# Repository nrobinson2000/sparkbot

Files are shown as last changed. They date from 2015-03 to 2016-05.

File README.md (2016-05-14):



# SparkBot: The IoT robotics kit for everyone

SparkBot is a robotics kit designed for makers and hobbyists, recommended for individuals aged 12 and up. It uses the Photon by Particle to teach C++ and principles of the Internet of Things. Its goal is to teach functional robotics, Arduino, and REST API's in an understandable method.

The purpose of SparkBot is to create a robot front end for the Photon that will get people excited to program and make projects with. It will give a reason for people to become interested in the Internet of Things by creating an exciting interactive experience.

SparkBot is a two part product. Although it uses both hardware and software from Particle, unique PCBs and 3D printed bodies must be produced. SparkBot also has its own software library with custom C++ functions to improve the SparkBot programming experience.

# The Photon:

The Photon is the SparkBot's brain. It runs C++ on its micro operating system, that communitcates with Particle's servers to create a low cost, high power device. Code can be uploaded to the Photon in several ways. Flashed from the [Particle.io web IDE][7], uploaded from either the Particle DEV IDE or the Particle CLI tool, or compiled locally and flashed over USB serial.

The Photon is Particle's second IoT development board. Their first was the Core, a huge Kickstarter success. The Photon was developed without any Kickstarter support, and the Electron, their third board, which uses celluar technology, was successfully funded on Kickstarter this year.

# Licensing:

SparkBot respects and uses many open source technologies and services. All of the software sources and hardware files can be found on GitHub.

[][8]  
SparkBot by [Nathan Robinson][9] is licensed under a [Creative Commons Attribution-NonCommercial-ShareAlike 4.0 International License][8].  
Based on a work at [https://github.com/nrobinson2000/sparkbot][2].

# Repositories:

SparkBot is organized into two repositories. One for the C++ library, and the other for everything else, including the hardware files, plans and images.

If you are looking for the C++ library for SparkBot, head over to [https://github.com/nrobinson2000/sparkbot-default][10]. The main repository is located at [https://github.com/nrobinson2000/sparkbot][2].

It is likely that a third repository will be created for the SparkBot documentation.

# Included in the SparkBot Kit:

* 1 Particle Photon
* 1 Micro usb cable
* 1 Half Breadboard
* 1 Fully assembled Robot body
* 10 Jumper wires
* 1 Protective travel case
* 1 User manual and quickstart guide

# Photon Pinout:
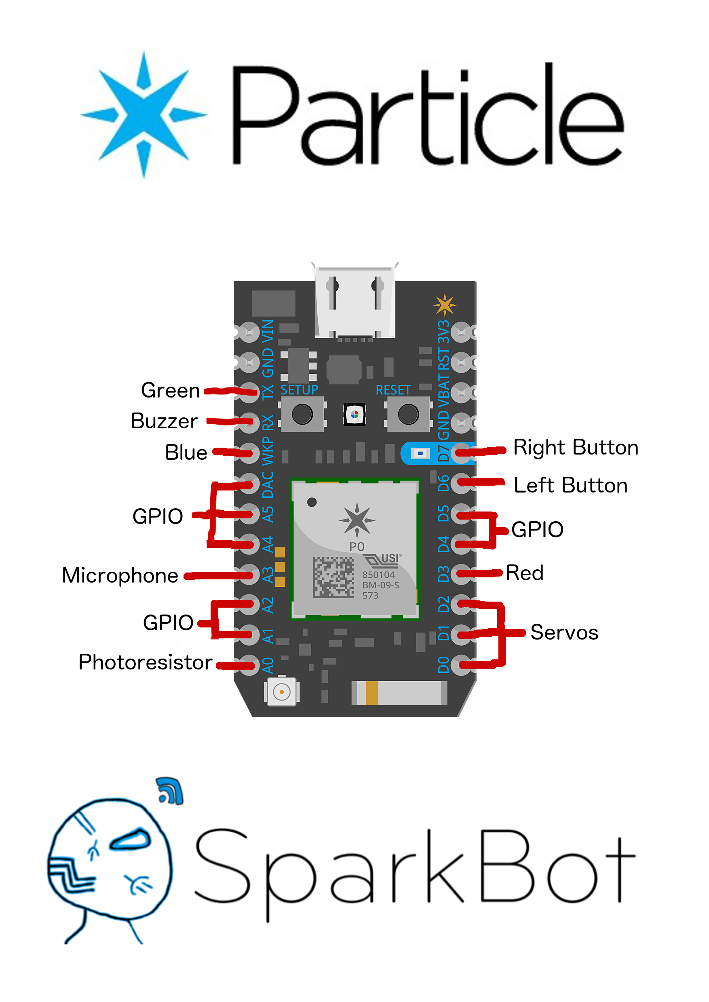
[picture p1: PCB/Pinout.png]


The SparkBot shield makes use of most of pins of the Photon, allowing it to work with all of the SparkBot components, as well as expose several pins for external GPIO.

# Purpose:

I created the idea for SparkBot back in 9th grade. I have been developing it since then, and have turned it into the base of my grade 10 pesonal project.

[0]: https://github.com/nrobinson2000/sparkbot/zipball/master
[1]: https://github.com/nrobinson2000/sparkbot/tarball/master
[2]: https://github.com/nrobinson2000/sparkbot
[4]: https://disqus.com/home/forums/sparkbot/
[5]: http://www.amazon.co.uk/registry/wishlist/1AIE1WKJD3ZFD
[6]: #sparkbot-the-iot-robotics-kit-for-everyone
[7]: https://build.particle.io/
[8]: http://creativecommons.org/licenses/by-nc-sa/4.0/
[9]: http://nrobinson2000.github.io/sparkbot/
[10]: https://github.com/nrobinson2000/sparkbot-default

<center>(https://nrobinson2000.github.io/donate-bitcoin/)</center>

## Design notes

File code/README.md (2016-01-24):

# Code

## This directory contains the code intended to run on the Arduino nano.  The Arduino nano acts as the brawns for my robot, as it controls the Servos and the RGB lights.

The Arduino nano communicates with the Photon over serial.  It can can take direct commands like setting to states of different pins or reading pins, and or advanced commands like running a certain light show or dance.

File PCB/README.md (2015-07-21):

#PCB
######This directory contains all of the Fritzing PCB files, concept designs, and PDF images of all the SparkBot PCBs.

* Main/ - This is the Main Spark Photon shield PCB.
* Others/ - These are the other PCBs used for SparkBot.  They include the 2 Button + RGB PCBs for the hands, the RGB PCB for the head, and the Photoresistor PCB.
* Backpacks/ - **NEW UPDATE!** This folder contains the designs for SparkBot Backpacks, which plug in directly to the back of the robot, and are great expansion boards.
* PCB Sketch.pdf: This was the original design idea for the SparkBot shield.

#PCB Pinout
* Buzzer = A4
* Microphone = A3
* Photoresistor = A0
* IO 0 = A6
* IO 1 = A1
* IO 2 = A2
* IO 3 = D5
* IO 4 = D4
* Right Servo = D0
* Left Servo = D1
* Neck Servo = D2
* Red LED = D3
* Blue LED = A5
* Green LED = A7
* Right Button = D7
* Left Button = D6

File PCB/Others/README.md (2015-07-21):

#Gerber Files
These folders contain the gerber files for the production of the other SparkBot PCBs.

* Gerbers/RGB_Button/ - This is the RGB + button PCB.  Two of these will be required per SparkBot.
* Gerbers/Dual_RGB/ - This is the dual RGB PCB.  One of these will be required.
* Gerbers/Photoresistor/ - This is the photoresistor PCB.  One of these will be required.

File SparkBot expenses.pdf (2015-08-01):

Sheet1

Description | Quantity | Price | Total
3 | $133.10
3 | $0.00 | $0.00
3 | $7.95 | $23.85
3 | $16.25
6 | $4.60
3 | $0.75
3 | $1.85
3 | $0.00 | $0.00
| | TOTAL | $180.40
| | | $60.13

I am going to buy the amount of parts to make three SpakBots.
SparkBot Expenses

Parts from
Digikey
Particle
Photon
Parts from
SparkFun
Main PCB
printed by
OSH Park
RGB Button
PCB printed
by OSH Park
Photresistor
PCB printed
by OSH Park
Dual RGB
PCB printed
by OSH Park
3D Printed
Body

Per
SparkBot

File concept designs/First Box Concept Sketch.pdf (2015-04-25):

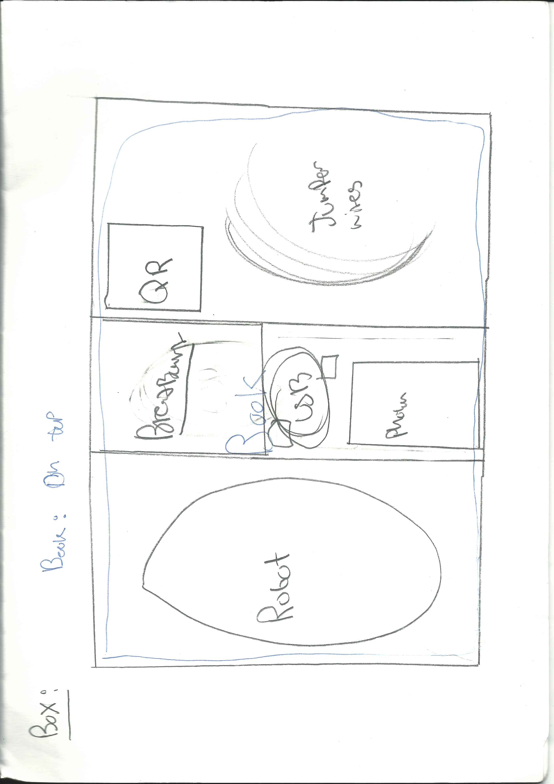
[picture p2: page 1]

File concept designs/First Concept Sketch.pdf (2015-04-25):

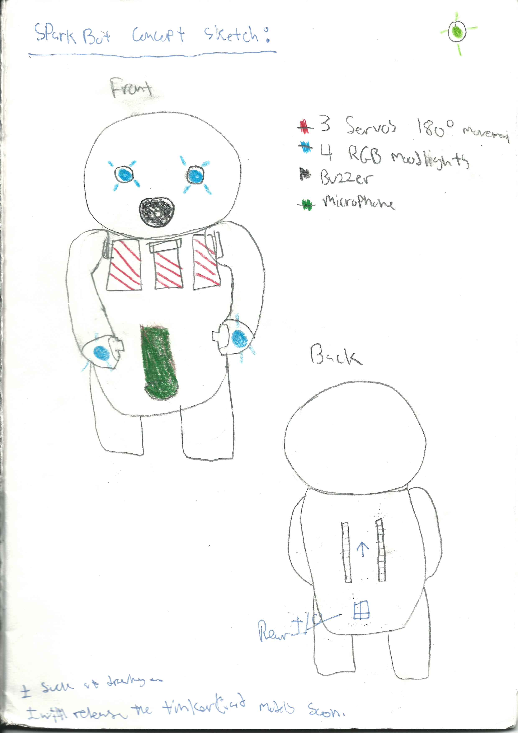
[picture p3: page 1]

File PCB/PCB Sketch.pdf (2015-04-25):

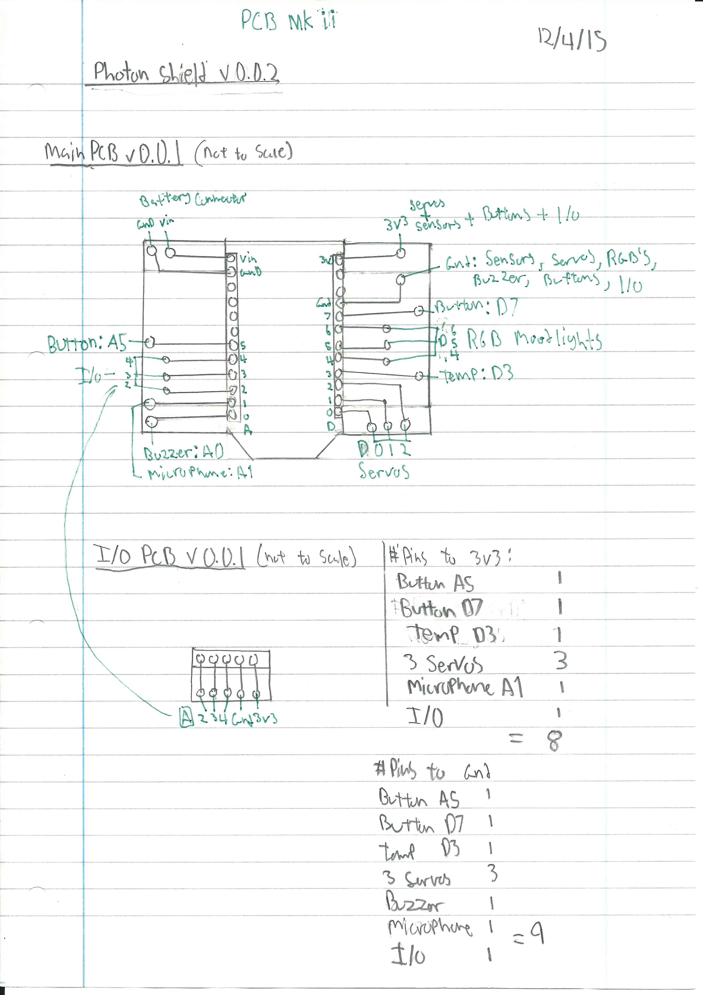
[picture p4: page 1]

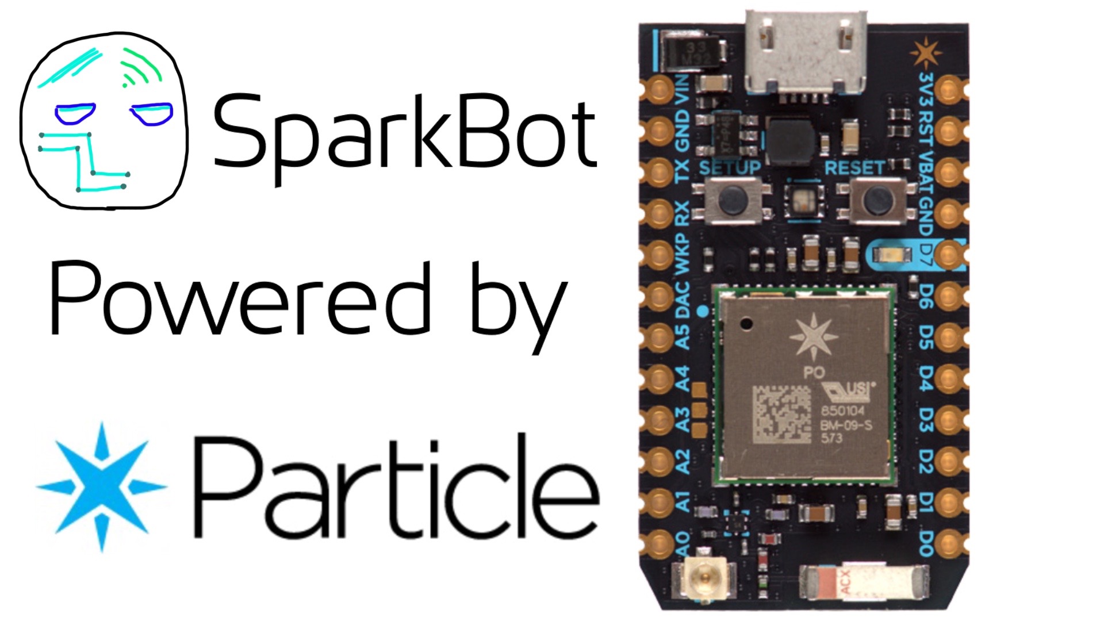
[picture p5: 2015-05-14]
kickstarter/Poster.jpg

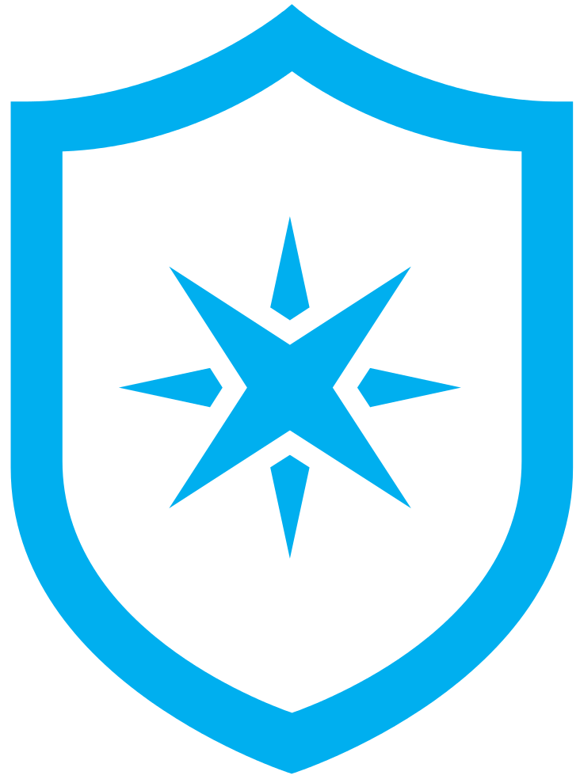
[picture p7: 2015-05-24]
reference/images/particle_shield.png

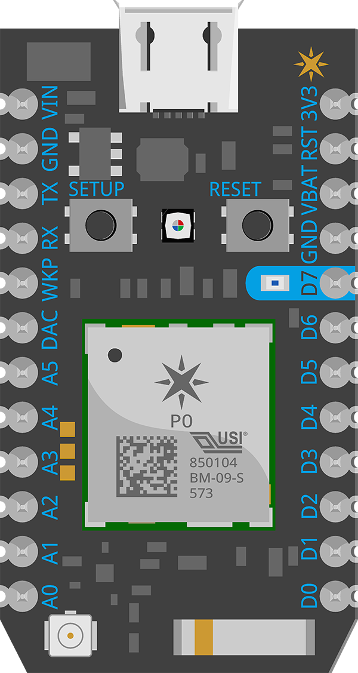
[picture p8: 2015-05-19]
kickstarter/photon_vector2_600.png

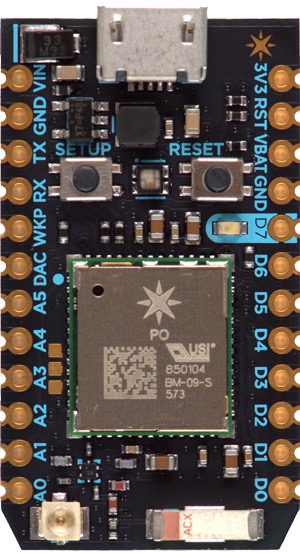
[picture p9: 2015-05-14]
kickstarter/Photon.jpg

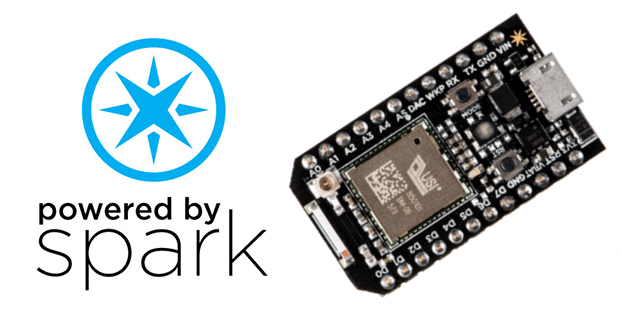
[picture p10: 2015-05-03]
marketing/PoweredBySpark.jpg

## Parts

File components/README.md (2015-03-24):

#SparkBot components
There are several different sensors and components that will be reqire to menufature the SparkBot.
Listed below is the components for the robot body + accessories.
**Prices correct on Amazon of March 23, 2015**
####**Estimated per unit manufacturing cost: £30**

####Components for each individual unit:
* 4 5mm Diameter Frosted Head 4 Pins RGB Light LED Diodes
* 1 DS18B20 Digital Temperature Sensor
* 1 Piezo Buzzer Electric Transducer
* 1 AD-037 High Sensitivity ECM Electret Condenser Microphone Sound Detecting Sensor Module
* 3 VicTsing 5 Pcs Mini SG90 9g Micro Servo Motor
* Male and Female headers
* 65 pcs Jumper Wire assortment
* 2 Quality Mini Micro Momentary Tactile Push Button Switches
* 1 Half Breadboard
* 1 Micro USB cable

####Links to parts on Amazon.co.uk:
* http://www.amazon.co.uk/Diameter-Frosted-Head-Light-Diodes/dp/B0087YR7UW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
* http://www.amazon.co.uk/Temperature-Sensor--Fit-Long-distance-Multipoint-Detention/dp/B0085QLYX8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
* http://www.amazon.co.uk/Piezo-Buzzer-Electric-Transducer-Arduino/dp/B00OS81QTO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
* http://www.amazon.co.uk/Sensitivity-Condenser-Microphone-Detecting-application/dp/B00Q2OD2OO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
* http://www.amazon.co.uk/VicTsing-Micro-Helicopter-Airplane-controls/dp/B00J593SKQ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
* http://www.amazon.co.uk/Female-Single-40-Square-Pin-Header-Components/dp/B008QUVM4E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
* http://www.amazon.co.uk/Reusable-Solderless-Breadboard-Circut-Creating--Assorted/dp/B008U4ZOLI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
* http://www.amazon.co.uk/Generic-Quality-Momentary-Tactile-Button/dp/B00D82M9LA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
* http://www.amazon.co.uk/BB400-Solderless-Plug--BreadBoard-tie-points/dp/B0040Z1ERO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
* http://www.amazon.co.uk/CHARGER-Samsung-ERICSSON-Incredible-BlackBerry-iZKA/dp/B004Z7D01K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

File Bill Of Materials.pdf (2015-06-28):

SparkBot BOM

PRODUCT NAME SparkBot
CURRENT DATE 14/05/15
Identifier | Description | Value | Designator | Quantity | Price | TOTAL
Photoresistor | LDR | 1 | $1.99 | $1.99
P1 | 1 | $3.62 | $3.62
| M1 | 1 | $7.95 | $7.95
Servo Motor Adafruit | H1, LE1, RI1, | 3 | $5.95 | $17.85
754-1615-ND RGB | 4 | $1.89 | $7.56
| | 450-1650-ND B1, B2 | 2 | $0.10 | $0.20
Resistor | 220 Ohms | S220HCT-ND R1 | 1 | $0.11 | $0.11
S7045-ND | J1, J2 | 2 | $1.01 | $2.02
S7007-ND | I/O | 1 | $0.94 | $0.94
H1, LE1, RI1, | 3 | $0.39 | $1.17
Jumper Wires | 1 | $3.18 | $3.18
377-2094-ND | 1 | $4.50 | $4.50
Q855-ND | 1 | $2.63 | $2.63
| 1 | $19.00 | $19.00

350-00009-
ND

Piezo Buzzer
Electric
Transducer

490-5958-1-
ND

SparkFun
Electret
Microphone
Breakout

htps://www.sparkfun.com/pr oducts/9964

1528-1076-
ND

RGB Light
LED Diodes

5mm
Diameter, 4
Pins

Mini Micro
Momentary
Tactile Push
Button Switch

Female
Headers (12
pos)

(0.1 inch
spacing)

Female
Headers (9
pos)

(0.1 inch
spacing)

Male
Headers(3
pos)

(0.1 inch
spacing)

S1012E-03-
ND

Pack of 10
(male to
male)

1471-1232-
ND

Half
Breadboard

Micro USB
Cable

Particle
Photon

SparkBot BOM

Main PCB | 1 | $13.45 | $13.45
Other PCBs | 1 | $7.47 | $7.47
Total: | $93.64
| | | $74.64

Without
Photon:

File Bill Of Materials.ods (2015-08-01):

PRODUCT NAME SparkBot
CURRENT DATE 30/07/15
Identifier | Description | Value | Designator | Quantity | Price | TOTAL
Photoresistor |  | 350-00009-ND | LDR | 1 | $1.99 | $1.99
Piezo Buzzer Electric Transducer |  | 490-5958-1-ND | P1 | 1 | $3.62 | $3.62
SparkFun Electret Microphone Breakout | https://www.sparkfun.com/products/9964 |  | M1 | 1 | $7.95 | $7.95
Servo Motor | Adafruit | 1528-1076-ND | H1, LE1, RI1, | 3 | $5.95 | $17.85
RGB Light LED Diodes | 5mm Diameter, 4 Pins | 754-1615-ND | RGB | 4 | $1.89 | $7.56
Mini Micro Momentary Tactile Push Button Switch |  | 450-1650-ND | B1, B2 | 2 | $0.10 | $0.20
Resistor | 220 Ohms | S220HCT-ND | R1 | 1 | $0.11 | $0.11
Female Headers (12 pos) | (0.1 inch spacing) | S7045-ND | J1, J2 | 2 | $1.01 | $2.02
Female Headers (9 pos) | (0.1 inch spacing) | S7007-ND | I/O | 1 | $0.94 | $0.94
Male Headers(3 pos) | (0.1 inch spacing) | S1012E-03-ND | H1, LE1, RI1, | 3 | $0.39 | $1.17
Jumper Wires | Pack of 10 (male to male) | 1471-1232-ND |  | 1 | $3.18 | $3.18
Half Breadboard |  | 377-2094-ND |  | 1 | $4.50 | $4.50
Micro USB Cable |  | Q855-ND |  | 1 | $2.63 | $2.63
Particle Photon |  |  |  | 1 | $19.00 | $19.00
Main PCB |  |  |  | 1 | $13.45 | $13.45
Other PCBs |  |  |  | 1 | $7.47 | $7.47
 |  |  |  |  | Total: | $93.64
 |  |  |  |  | Without Photon: | $74.64

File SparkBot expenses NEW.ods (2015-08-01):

I am going to buy the amount of parts to make three SpakBots.
SparkBot Expenses
Description | Quantity | Price | Total
Parts from Digikey | 3 |  | $133.10
Particle Photon | 3 | $0.00 | $0.00
Parts from SparkFun | 3 | $7.95 | $23.85
Main PCB printed by OSH Park | 3 |  | $16.25
RGB Button PCB printed by OSH Park | 6 |  | $4.60
Photresistor PCB printed by OSH Park | 3 |  | $0.75
Dual RGB PCB printed by OSH Park | 3 |  | $1.85
3D Printed Body | 3 | $0.00 | $0.00
 |  | TOTAL | $180.40
 |  | Per SparkBot | $60.13

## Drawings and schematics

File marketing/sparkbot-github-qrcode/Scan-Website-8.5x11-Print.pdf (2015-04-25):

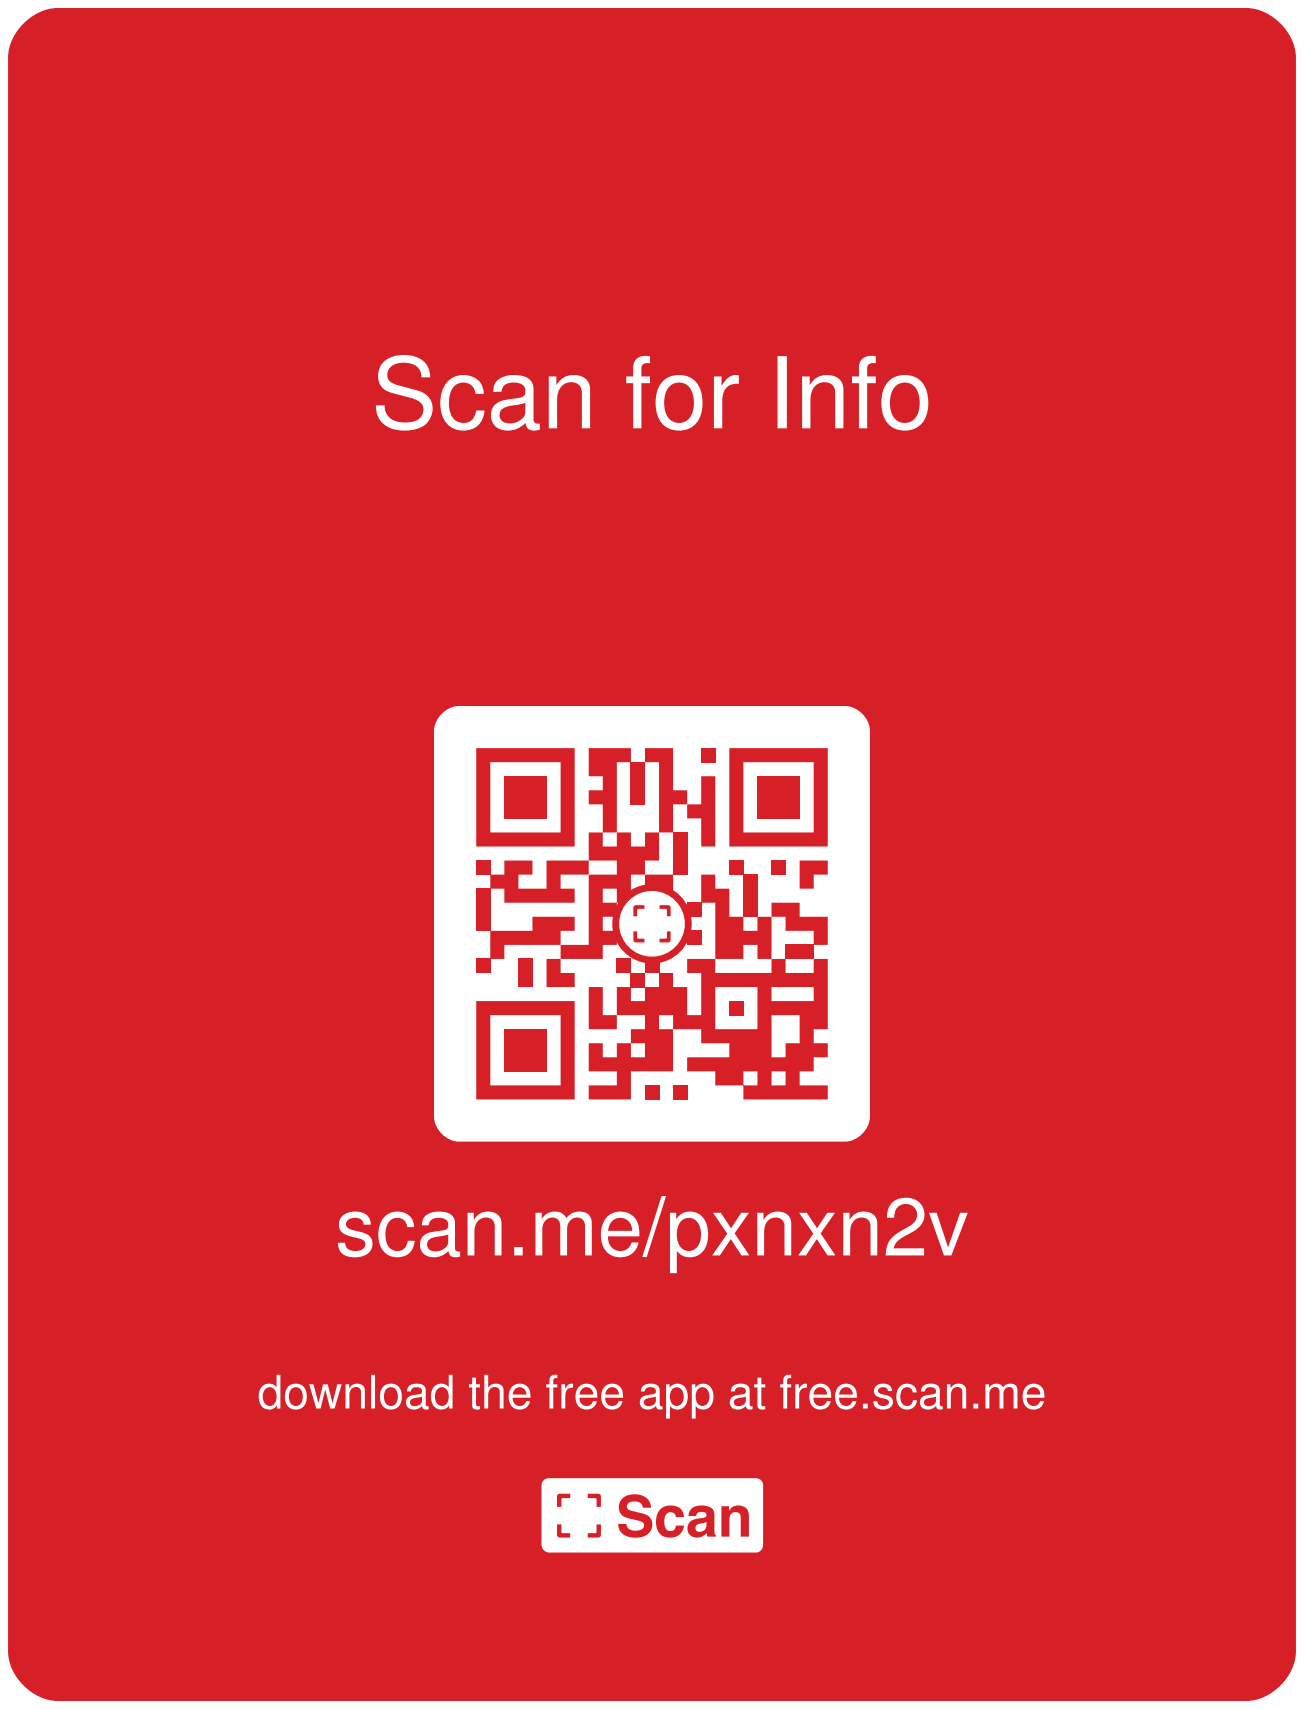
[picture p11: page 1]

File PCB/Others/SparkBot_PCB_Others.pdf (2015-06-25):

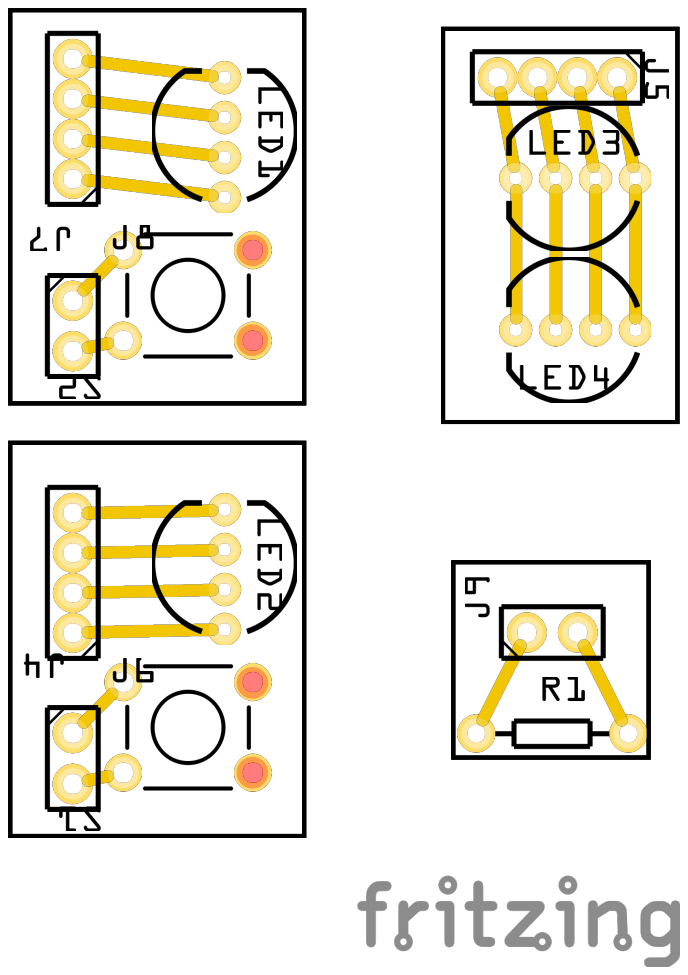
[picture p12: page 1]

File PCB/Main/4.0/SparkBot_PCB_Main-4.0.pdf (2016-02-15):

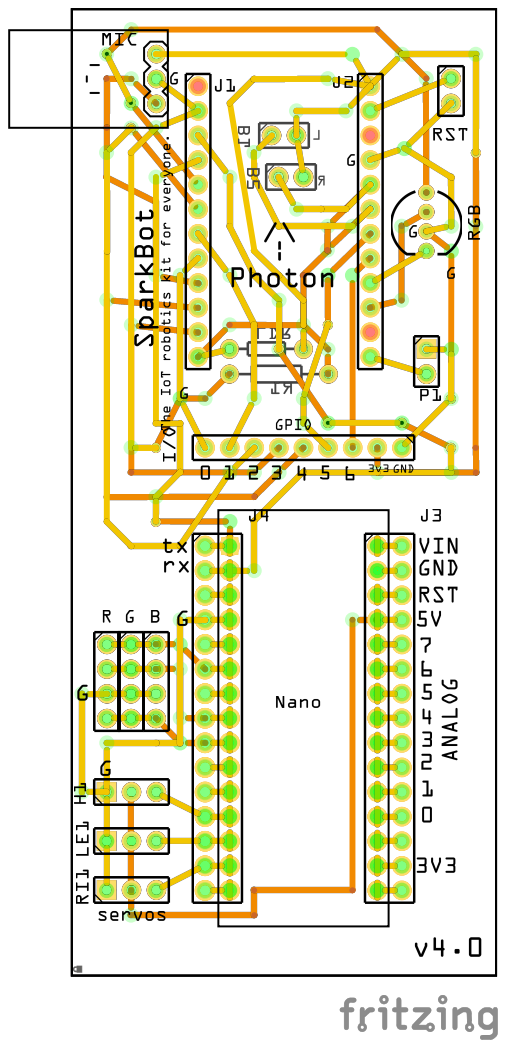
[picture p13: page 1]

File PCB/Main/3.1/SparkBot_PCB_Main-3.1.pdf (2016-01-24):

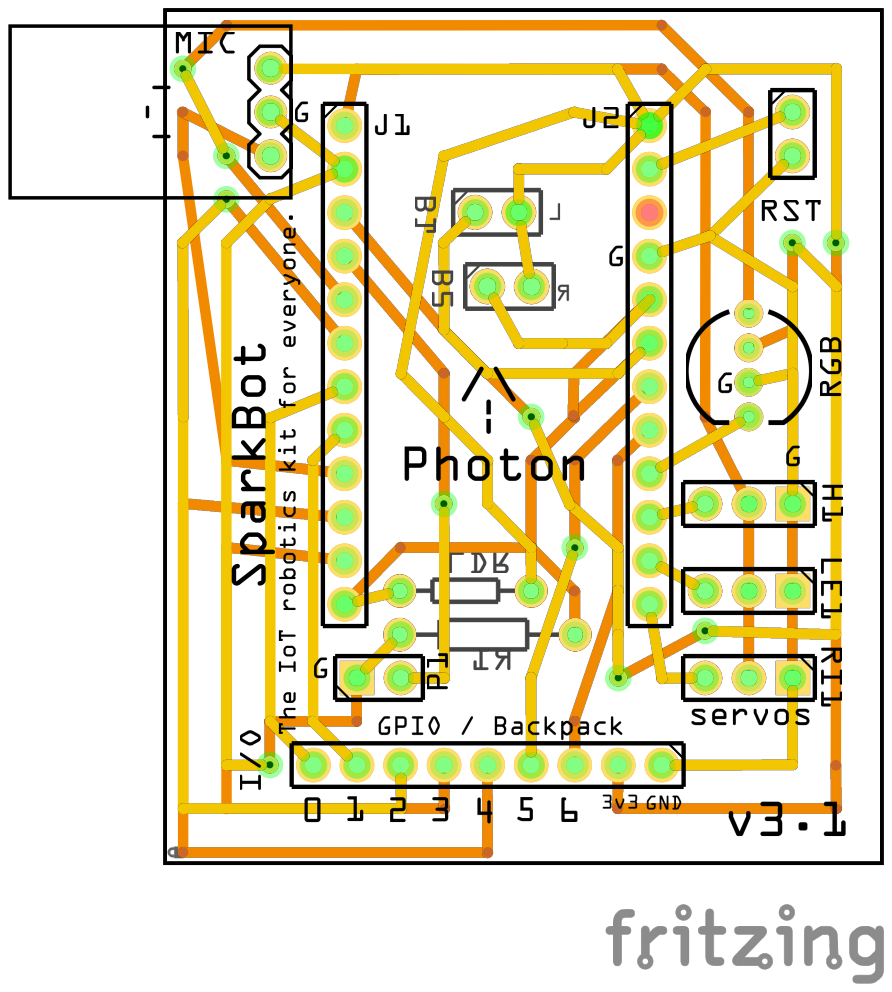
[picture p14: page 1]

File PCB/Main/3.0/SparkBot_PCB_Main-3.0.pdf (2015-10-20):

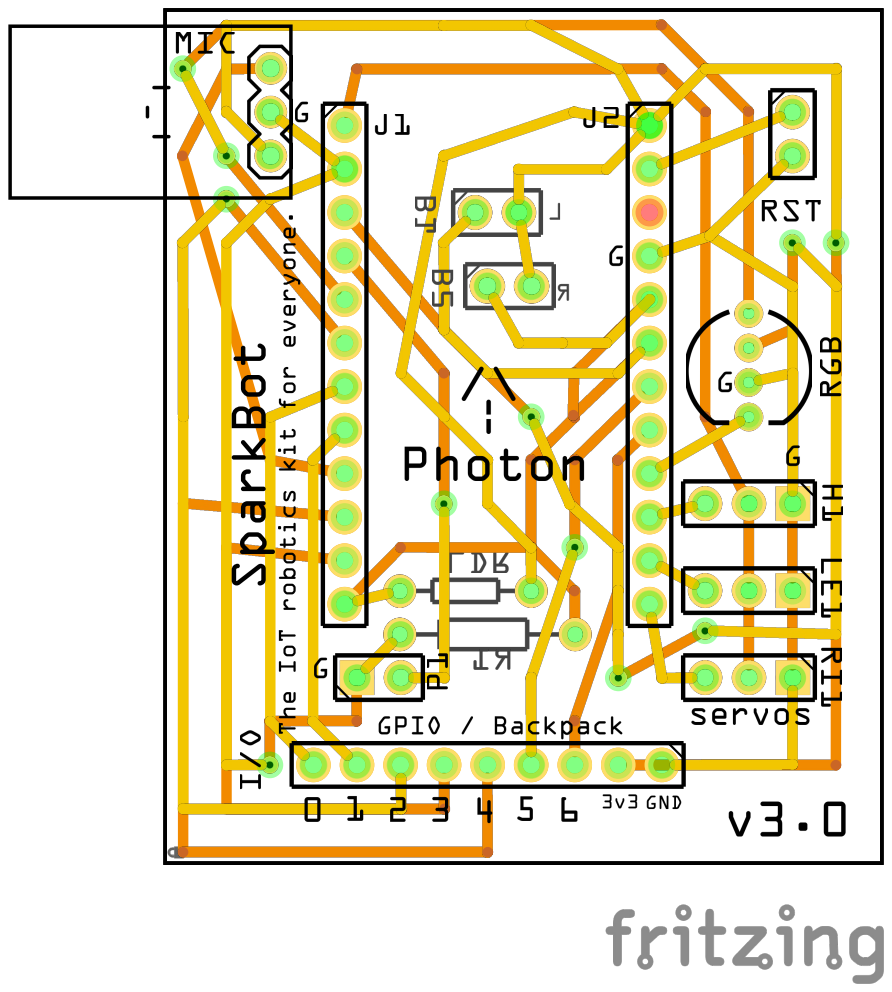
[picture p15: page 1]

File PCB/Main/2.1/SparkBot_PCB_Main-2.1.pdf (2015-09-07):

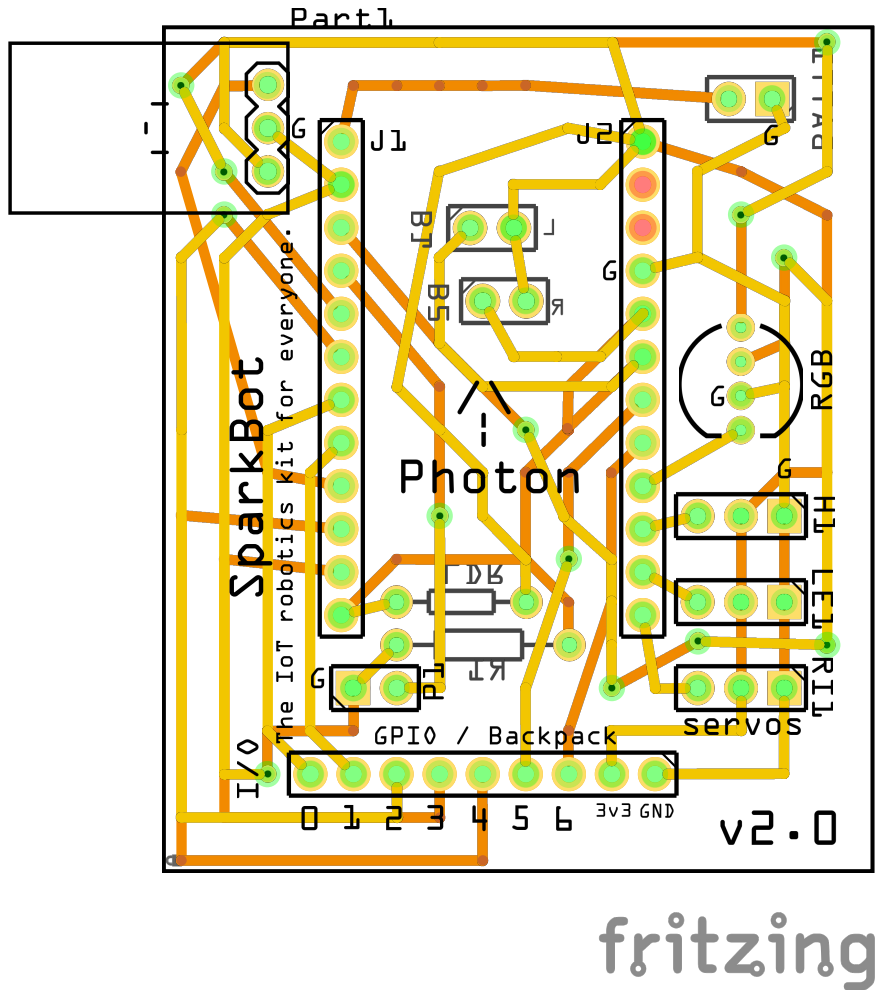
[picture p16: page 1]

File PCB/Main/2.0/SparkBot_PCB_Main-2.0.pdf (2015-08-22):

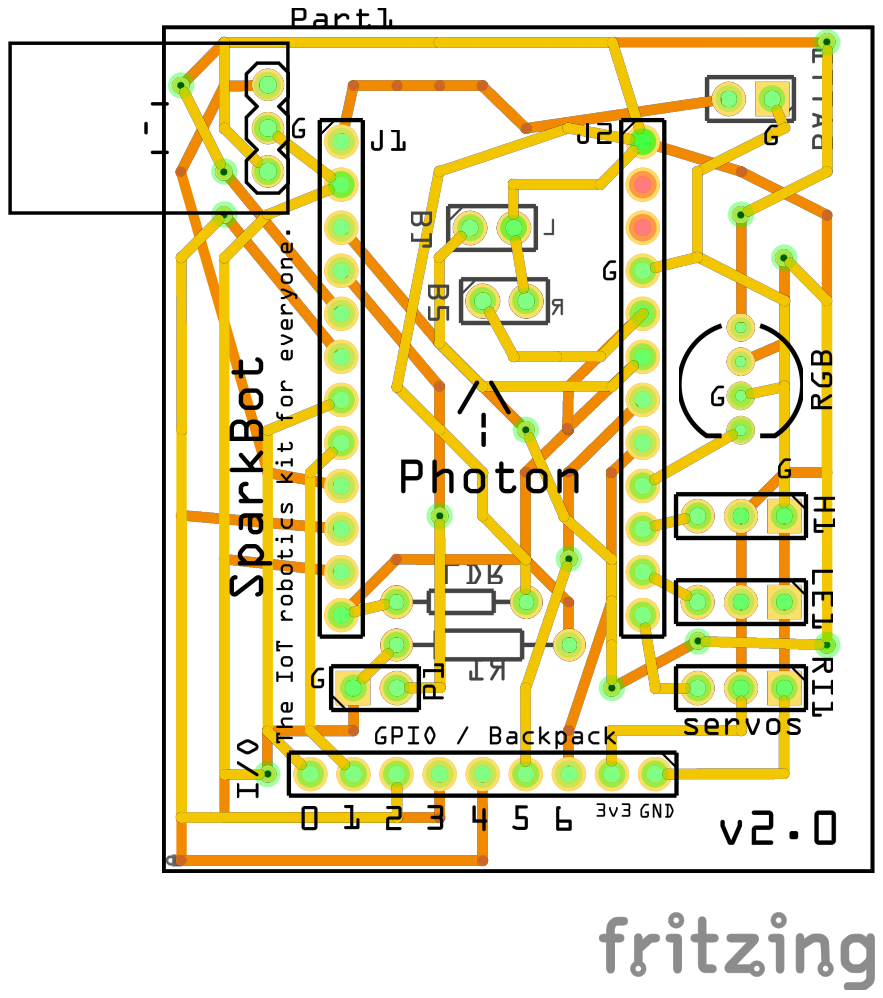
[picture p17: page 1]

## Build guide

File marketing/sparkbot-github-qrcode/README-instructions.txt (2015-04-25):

Here are some simple tips and instructions on how to best use your new QR code:

Scan-Website-8.5x11-Print.pdf - Best for instant printing on standard 8.5x11 paper.

Scan-Website-Badge-Red.jpg - Great for posters, flyers, and other print materials.

Scan-Website-Badge-Gray.jpg - Great for posters, flyers, and other print materials.

Scan-Website-Badge-Red.png - Great for blogs, social networks, videos, and other digital media.

Scan-Website-Badge-Gray.png - Great for blogs, social networks, videos, and other digital media.

Scan-Website-Color.jpg - Great for posters, flyers, and other print materials.

Scan-Website-Gray.jpg - Great for posters, flyers, and other print materials.

Scan-Website-Color.png - Great for blogs, social networks, videos, and other digital media.

Scan-Website-Gray.png - Great for blogs, social networks, videos, and other digital media.

Scan-Website-Vector-Set.eps - We've included your code in a vector format to give you complete freedom and control over customization. Great for large signs, embroidery, custom designs, and really whatever you can imagine!

Questions? We'd love to help you out. You can reach us at help@scan.me
Check out other great examples and best practices in our gallery : http://scan.me/gallery

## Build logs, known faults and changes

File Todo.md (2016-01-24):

#SparkBot Todo List:

# Notes:
* Explain why I am using GitHub over Google Drive,
* Explain why I made my own PCB over using a Breadboard.
* Explain why I made my own website over the standard template.
* Talk about challenges.  PWMS, PCB, 3D Models

## Project:
* Explain why I am using GitHub over Google Drive.

## Website:
* Explain why I am using my own Website over Google Sites.
* Condense information on website, (break it into sections.)

## Reflection:
* Talk about challenges.  (Not enough PWMs, Designing my own PCB, Creating my 3D Models, Paying more for shipping than the components.)
* Comercial Aspect

* [ ] Assemble SparkBot electronics and PCBs
* [ ] Debug C++ library
* [ ] Design 3D models for SparkBot body (using Blender?)
* [ ] 3D print prototype models
* [ ] Assemble full SparkBot prototypes
* [ ] Start writing user manual and create documentation website
* [ ] Design and create packaging prototypes
* [ ] Get logo from 99Designs
* [ ] Create SparkBot community and get supporters
* [ ] Launch Kickstarter campaign?

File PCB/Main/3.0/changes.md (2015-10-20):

# Changes:

* Swapped 3v3 with VIN on the servos.  I am expecting this to supply the servos with > 4.5 volts.  I expect this to fix problems I was having with my servos.
* Removed the pins for attaching a 9V battery pack.
* Added pins to solder an external reset button.
* Cleaned up some connections.

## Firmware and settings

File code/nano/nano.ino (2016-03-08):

// This file needs to be flashed to the Nano in the Arduino IDE.  Just open the "nano" directory and flash.
#include <Servo.h>

int redled = 6;
int greenled = 3;
int blueled = 5;

Servo neckservo;
Servo leftservo;
Servo rightservo;

String readString;

void setup()
{
  Serial.begin(9600);

  neckservo.attach(9);
  leftservo.attach(10);
  rightservo.attach(11);

  pinMode(redled, OUTPUT);
  pinMode(greenled, OUTPUT);
  pinMode(blueled, OUTPUT);
}

void loop()
{

  while (Serial.available())
  {
    delay(3);
    char c = Serial.read();
    readString += c;
  }

  readString.trim();

  if (readString.length() > 0)
  {
    parseCommand(readString);

    readString = "";
  }
}

int parseCommand(String command)
{
  Serial.println(command);

  //  if (command.startsWith("servo"))
  //  {
  //    String servoValues = command.substring(6);
  //    moveServos(servoValues);
  //  }

  if (command.startsWith("rgb"))
  {
    String rgbValues = command.substring(4);
    changeRGB(rgbValues);
  }

  if (command.startsWith("moveNeck"))
  {
    String servoValues = command.substring(9);
    moveNeck(servoValues.toInt());
  }

  if (command.startsWith("moveLeft"))
  {
    String servoValues = command.substring(9);
    moveLeft(servoValues.toInt());
  }

  if (command.startsWith("moveRight"))
  {
    String servoValues = command.substring(10);
    moveRight(servoValues.toInt());
  }

  if (command.startsWith("servos"))
  {
    Serial.println("servos " + makeProper(neckservo.read()) + " " + makeProper(leftservo.read()) + " " + makeProper(rightservo.read()));
  }

  if (command.startsWith("neck"))
  {
    Serial.println("neck " + String(neckservo.read()));
  }

  if (command.startsWith("left"))
  {
    Serial.println("left " + String(leftservo.read()));
  }

  if (command.startsWith("right"))
  {
    Serial.println("right " + String(rightservo.read()));
  }

}

void moveNeck(int value)
{
  neckservo.write(value);
  delay(2);
}

void moveLeft(int value)
{
  leftservo.write(value);
  delay(2);
}

void moveRight(int value)
{
  rightservo.write(value);
  delay(2);
}

int changeRGB(String data)
{
  String red = data.substring(0, 3);
  String green = data.substring(4, 7);
  String blue = data.substring(8, 11);

  if (red.toInt() != 300)
  {
    analogWrite(redled, red.toInt());
  }
  if (green.toInt() != 300)
  {
    analogWrite(greenled, green.toInt());
  }
  if (blue.toInt() != 300)
  {
    analogWrite(blueled, blue.toInt());
  }
}

String makeProper(int value)
{
  String valuedata;
  if (value < 100 && value > 9)
  {
    valuedata = String("0" + String(value));
  }
  if (value < 10)
  {
    valuedata = String("00" + String(value));
  }
  else
  {
    valuedata = String(value);
  }

  return valuedata;
}

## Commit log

2015-03-26 Added Sparkbot
    [SparkBot-main.fzz]
2015-05-11 Beginning to make BOM
    [Bill Of Materials.ods, SparkBot_PCB_Main.fzz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]
2015-05-11 update
    Changed pin configuration. Now using analog thermometer.
    [Bill Of Materials.ods, SparkBot_PCB_Main.fzz]
2015-05-14 New Pinout
    [SparkBot_PCB_Main.fzz]
2015-05-14 rotated pcb
    [SparkBot_PCB_Main.fzz]
2015-05-16 Fix pins
    [SparkBot_PCB_Main.fzz]
2015-05-16 Removed button resistors
    [SparkBot_PCB_Main.fzz]
2015-05-16 Removed resistors
    [Bill Of Materials.ods]
2015-05-16 Updated Main Gerber files
    [SparkBot_PCB_Main_copperBottom.gbl, SparkBot_PCB_Main_copperTop.gtl, SparkBot_PCB_Main_maskBottom.gbs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]
2015-05-16 Updates
    Added Open hardware logo
    [SparkBot_PCB_Main.fzz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]
2015-05-17 PCB update. Added silkscreen ground labels.
    [SparkBot_PCB_Main.fzz]
2015-05-17 New components
    [Bill Of Materials.ods]
2015-05-18 Fix: added resistor
    [Bill Of Materials.ods, SparkBot_PCB_Main.fzz]
2015-05-18 Derp. Fixed missing wire
    [SparkBot_PCB_Main.fzz]
2015-05-19 Swapped Servo pins with RGB pins so that the RGB will be on PWM outputs, allowing the lights to dim.
    [SparkBot_PCB_Main.fzz]
2015-05-28 Updated PCB With logo
    [SparkBot_PCB_Main.fzz]
2015-05-28 Added photresistor
    [Bill Of Materials.ods]
2015-06-20 Updated with pcb costs
    [Bill Of Materials.ods]
2015-06-24 New pinout released, changes made to PCB and code
    [SparkBot_PCB_Main.fzz]
2015-06-25 Update at 14:55 of 25-06-2015
    [SparkBot_PCB_Main.fzz]
2015-06-25 Update at 15:35 of 25-06-2015
    [SparkBot_PCB_Main.fzz, SparkBot_PCB_Others.fzz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]
2015-06-26 Update at 19:52 of 26-06-2015
    [SparkBot_PCB_Others.fzz]
2015-06-26 Update at 20:20 of 26-06-2015
    [Bill Of Materials.ods]
2015-06-27 Update at 12:28 of 27-06-2015
    [Bill Of Materials.ods, SparkBot_PCB_Main.fzz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]
2015-06-27 Update at 00:32 of 28-06-2015
    [SparkBot_PCB_Main.fzz]
2015-06-28 Update at 16:52 of 28-06-2015
    [Bill Of Materials.ods]
2015-06-29 Updated PCB
    [SparkBot_PCB_Main.fzz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]
2015-06-29 Update PCB
2015-07-21 BackPack Update!
    [Potentiometers.fzz, SparkBot_PCB_Main.fzz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]
2015-07-24 Removed duplicate .fzz file
    [SparkBot_PCB_Main.fzz]
2015-07-26 PCB update
    [SparkBot_PCB_Main.fzz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]
2015-07-31 Update at 22:01 of 31-07-2015
    [Bill Of Materials.ods]
2015-08-01 Update at 13:15 of 01-08-2015
    [SparkBot expenses NEW.ods]
2015-08-01 Update at 13:28 of 01-08-2015
    [Bill Of Materials.ods]
2015-08-01 Update at 13:39 of 01-08-2015
    [SparkBot expenses NEW.ods]
2015-08-04 Update at 12:24 of 04-08-2015
    [SparkBot_PCB_Main.fzz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]
2015-08-22 Created Main PCB v2.0 to slove problem with pwm pins.
    [SparkBot_PCB_Main-2.0.fzz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]
2015-09-02 Updated pcb to 2.1
    [SparkBot_PCB_Main-2.0.fzz]
2015-10-18 13:55 of 18-10-2015
    [SparkBot_PCB_Main-3.0.fzz]
2015-10-18 PCB 3.0 16:10 of 18-10-2015
    [SparkBot_PCB_Main-3.0.fzz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]
2015-10-20 New PCB 3.0 11:47 of 20-10-2015
    [SparkBot_PCB_Main-3.0.fzz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]
2015-12-04 Got pcb. Pcb didn't work because of 3v3 went do a ground pin. Fixed problem with gerbers. Going to order new pcb soon. 20:53 of 04-12-2015
    [SparkBot_PCB_Main-3.1.fzz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]
2015-12-06 Fixed pcb http://nrobinson2000.github.io/sparkbot/#comment-2394613354 10:36 of 06-12-2015
    [SparkBot_PCB_Main-3.1.fzz]
2016-01-24 Working on new 4.0 PCB
    [SparkBot_PCB_Main-3.1.fzz, SparkBot_PCB_Main-4.0.fzz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]
2016-02-14 Added code for NANO and added gerbers for new PCB 14:22 of 14-02-2016
2016-02-14 Added code for NANO and added gerbers for new PCB 14:23 of 14-02-2016
    [SparkBot_PCB_Main-4.0.fzz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]
2016-02-15 11:59 of 15-02-2016
    [SparkBot_PCB_Main-4.0.fzz]
2016-02-27 Built PCB and fixed code. 16:00 of 27-02-2016
    [nano.ino]
